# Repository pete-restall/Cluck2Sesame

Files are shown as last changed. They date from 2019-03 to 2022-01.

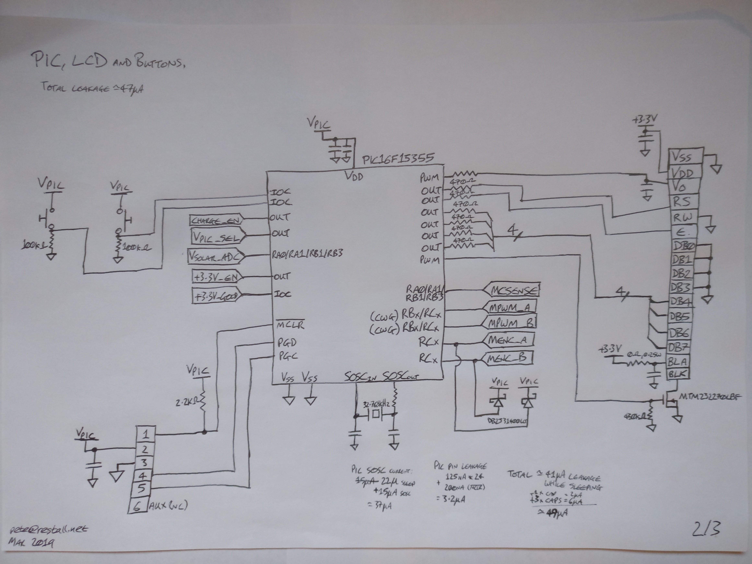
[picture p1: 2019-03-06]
doc/design/sketches/rough-circuit-outline-2.jpg

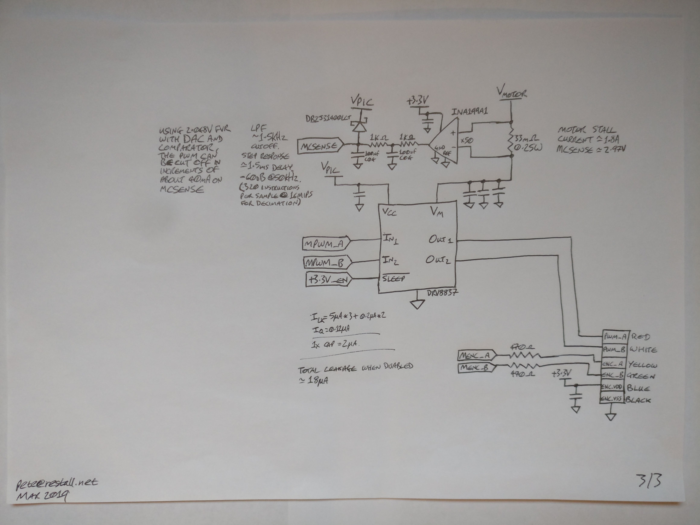
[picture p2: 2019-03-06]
doc/design/sketches/rough-circuit-outline-3.jpg

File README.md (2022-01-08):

# Cluck<sup>2</sup>Sesame - Yet Another Chicken Coop Door Opener (Revision II)

## What is it ?
It opens and closes the door of my wife's chicken coop based on Sunrise and
Sunset times so that she doesn't have to.  This is a refinement of the
[Cluck<sup>2</sup>Sesame](https://github.com/pete-restall/Cluck2Sesame-Prototype/)
project, building on lessons learned from the original attempt.  Notably:

 - The parts are not based on what I have lying around, but rather on parts
   selected for the job or known to do the job.  This has also simplified the
   design somewhat - more pins on the PIC mean the shift register is no longer
   required, for example.  The newer PIC is smaller, integrates more
   peripherals and comes with more flash; the original project ran out of
   flash before all features could be implemented.

 - The shortcomings in the end-of-travel detection, namely measuring motor
   current for stall torque, hastened battery depletion.  A rotary-encoder
   based approach will be used instead, which will hopefully lengthen battery
   life.

 - A solar charger will be included as replacing the battery, fairly regularly
   as it turned out, meant unscrewing the enclosure.

 - The motor will be a 6V model rather than a 12V model and run directly from 
   the battery rather than off an SMPS.  No SMPS means a smaller BOM and no
   power wasted by the high motor currents.  This should extend battery life
   even further, at the expense of varying speed.  But that's not an issue.

 - The PCB will be made in China, and the board house charges the same price
   regardless of whether the PCB is the size of the enclosure or the size of
   the LCD module.  This means that the aluminium backplate can be replaced
   with a PCB, providing more flexibility and space for layout and mounting
   while reducing the cost and time of the build.

That said, some of the parts from the original have been incorporated into
the newer design since they are known to work and are already stocked in my
parts bins.

## Why 'Cluck<sup>2</sup>Sesame' ?
Because 'Cluck Cluck Sesame' is obviously what the chickens would say if
they needed to open a door.

## The Hardware and Firmware
The hardware and firmware are all mine.  The board is based around a
[PIC16F15356](doc/datasheets/mcu/PIC16F15356.pdf).  It's a beefier evolution
of what was used last time that has allowed considerable simplification of the
board through more integration and a higher pin count.

## Pictures
None yet.  But there will be.

## Build


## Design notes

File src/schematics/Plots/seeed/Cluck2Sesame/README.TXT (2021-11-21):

Customer:
---------
Pete Restall (Parity Computer Consultancy Limited) - pete@restall.net
Any problems / questions, please do not hesitate to get in touch.

Design Tools Used:
------------------
DesignSpark 8.1.2
Gerbv 2.6.2

Track and Spacing:
------------------
Minimum 6mil.

Layers:
-------
All viewed from above, no mirroring.  Solder Resist and Solder Paste Stencil
layers are negatives, all others are positives.

Board Outline:
--------------
All layers contain a zero-width board outline.  Outline size is
4.24016in x 4.20000in and >= 20mil from any feature, copper or otherwise.

Vias and Silkscreen:
--------------------
Some vias are partially covered with silkscreen; this is not anticipated to
be an issue since they should be tented.

Pads and Silkscreen:
--------------------
Some silkscreen map overlap, but this is not an issue.  The silkscreen can be
clipped where necessary, but please advise if this is going to be an issue.

Drill Holes:
------------
All are through-plated and are finished sizes; no adjustments have been made
for plating thickness.  All are >= 20mil from the edge of the board.

Bit sizes can be rounded to the nearest 0.1mm.  Please advise if any drill
sizes are found to be incompatible with your processes.

Annular rings >= 6mil.  Holes >= 0.4mm.

Data Formats:
-------------
More detailed information can be found in "DesignSpark Plot Report.TXT", but
in summary:

Gerber Settings
===============

    Leading zero suppression.
    G01 assumed throughout.
    Line termination <*> <CR> <LF>.
    3.5 format absolute inches.
    Format commands defined in Gerber file.
    Aperture table defined in Gerber file.
    Hardware arcs allowed.

Drill Settings
==============

    Excellon Format 1
    Format 3.5 absolute in inches.
    Zero suppression Leading

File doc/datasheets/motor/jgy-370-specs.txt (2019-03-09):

=======================
From Aliexpress Website
=======================
1pcs DC6V 12V 24V JGY370 Large Torque Full Metal Gearbox Turbo Worm Gear Motor with Hall Encoder
Specification:
Note: Different parameters' motors have their different looks. The lower speed and higher voltage are, the larger the torque is. Please read the parameters table before buying. Thanks!!!

Voltage: DC6V, DC12V, DC24V

No-Load Speed: 6rpm, 10rpm, 18rpm, 23rpm, 30rpm, 40rpm, 90rpm, 150rpm

Error: ±10%

Output Shaft Diameter: 6mm D-type

Output Shaft Length: 14mm
Gearbox Size:46*32*25mm

Gearbox Size Detal, please see the table
Wirings:

Notice:  
1. The yellow and green wires are the speed signal output line, and they can't be connected any power supply, or it will be burnt.
2. Positive and negative power supply of encoder do not allow connect wrong;voltage is 3.3-5V.
3. Control CW or CCW of motor by changing the positive and negative power supply of encoder (change Red Wire and White Wire connect)

Red Wire - positive power supply of motor(+)

White Wire - negative power supply of motor(-)

Black Wire - negative power supply of encoder(-) (positive and negative power supply of encoder do not allow connect wrong;voltage is3.3-5V)

Blue Wire - positive power supply of encoder(+) (positive and negative power supply of encoder do not allow connect wrong;voltage is 3.3-5V)

Yellow Wire - signal feedback (11 signals per motor turns a circle)

Green Wire - signal feedback (11 signals per motor turns a circle)

========================
Measurements and Testing
========================
At 11 Celsius:

	+6.0V, 150mA unloaded, unable to stall with fingers
	+4.3V, 150mA unloaded, 1.5A stall
	+3.0V, 110mA unloaded, 900mA stall
	+2.5V, 100mA unloaded, 770mA stall
	+2.0V,  80mA unloaded, 615mA stall

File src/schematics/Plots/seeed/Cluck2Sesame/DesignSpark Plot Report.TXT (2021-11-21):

Plot Report
-----------

Report Written:     Sunday, November 21, 2021
Project Path:       Z:\home\pete\Projects\Cluck3Sesame\src\schematics\Cluck2Sesame.prj
Design Path:        Z:\home\pete\Projects\Cluck3Sesame\src\schematics\Cluck2Sesame.pcb
Design Title:       Cluck2Sesame PCB Layout
Created:            27/03/2019 19:50:45
Last Saved:         21/11/2021 18:45:09
Editing Time:       6089 min
Units:              mil (precision 2)

Device Settings
===============

Gerber Settings
===============

    Leading zero suppression.
    G01 assumed throughout.
    Line termination <*> <CR> <LF>.
    3.5 format absolute inches.

    Format commands defined in Gerber file.
    Aperture table defined in Gerber file.
    Hardware arcs allowed.

Drill Settings
==============

    Excellon Format 1    Format 3.5 absolute in mm.
    Zero suppression Leading

Plots Output
============

    Plot Job: "Z:\home\pete\Projects\Cluck3Sesame\src\schematics\Cluck2Sesame.mop"

Gerber Output
=============

Z:\home\pete\Projects\Cluck3Sesame\src\schematics\Plots\Cluck2Sesame - Top Silkscreen.gbr

    Layers:
    ------------------
    Top Silkscreen
    Board Outlines

    D-Code Shape  (thou)
    -----------------------
    D10    Round 5.00
    D11    Round 12.00
    D13    Round 0.00
    D77    Round 6.00
    D78    Round 20.00
    D79    Round 10.00

Gerber Output
=============

Z:\home\pete\Projects\Cluck3Sesame\src\schematics\Plots\Cluck2Sesame - Top Solder Mask.gbr

    Layers:
    -------------------
    Top Solder Mask
    Board Outlines

    D-Code Shape  (thou)
    ------------------------------------------
    D13    Round 0.00
    D80    Round 282.00
    D81    Round 216.00
    D82    Round 163.48
    D83    Square 74.00
    D84    Oval 68.99 X 100.49
    D85    Oval 66.00 X 116.00  Rotation 90
    D86    Square 69.00
    D87    Square 68.99

Gerber Output
=============

Z:\home\pete\Projects\Cluck3Sesame\src\schematics\Plots\Cluck2Sesame - Top Copper.gbr

    Layers:
    ------------------
    Top Copper
    Board Outlines

    D-Code Shape  (thou)
    ------------------------------------------
    D10    Round 5.00
    D11    Round 12.00
    D13    Round 0.00
    D88    Round 276.00
    D89    Round 210.00
    D90    Round 157.48
    D91    Square 68.00
    D92    Oval 62.99 X 94.49
    D93    Oval 60.00 X 110.00  Rotation 90
    D94    Square 63.00
    D95    Square 62.99
    D96    Round 28.00
    D97    Round 8.00

Gerber Output
=============

Z:\home\pete\Projects\Cluck3Sesame\src\schematics\Plots\Cluck2Sesame - Bottom Copper.gbr

    Layers:
    ------------------
    Bottom Copper
    Board Outlines

    D-Code Shape  (thou)
    ----------------------------------------------
    D10    Round 5.00
    D11    Round 12.00
    D13    Round 0.00
    D77    Round 6.00
    D78    Round 20.00
    D79    Round 10.00
    D88    Round 276.00
    D89    Round 210.00
    D90    Round 157.48
    D91    Square 68.00
    D92    Oval 62.99 X 94.49
    D93    Oval 60.00 X 110.00  Rotation 90
    D94    Square 63.00
    D95    Square 62.99
    D96    Round 28.00
    D97    Round 8.00
    D98    Rectangle 55.00 X 60.00
    D99    Rectangle 55.00 X 60.00  Rotation 90
    D100   Rectangle 9.06 X 27.56  Rotation 90
    D101   Rectangle 35.43 X 59.06
    D102   Rectangle 16.54 X 27.56
    D103   Rectangle 16.54 X 39.37
    D104   Rectangle 72.83 X 93.31  Rotation 90
    D105   Rectangle 31.50 X 35.43  Rotation 90
    D106   Rectangle 17.72 X 57.09
    D107   Rectangle 31.50 X 35.43
    D108   Round 9.84
    D109   Rectangle 7.87 X 31.50  Rotation 90
    D110   Rectangle 7.87 X 31.50
    D111   Square 92.52
    D112   Rectangle 23.62 X 47.24
    D113   Rectangle 35.43 X 35.43  Rotation 90
    D114   Rectangle 35.43 X 35.43
    D115   Rectangle 11.02 X 19.69  Rotation 90
    D116   Rectangle 35.43 X 62.99
    D117   Rectangle 15.75 X 23.62  Rotation 90
    D118   Rectangle 39.37 X 42.91  Rotation 90
    D119   Round 50.00
    D120   Round 9.00
    D121   Round 15.00

Gerber Output
=============

Z:\home\pete\Projects\Cluck3Sesame\src\schematics\Plots\Cluck2Sesame - Bottom Solder Mask.gbr

    Layers:
    ----------------------
    Bottom Solder Mask
    Board Outlines

    D-Code Shape  (thou)
    ----------------------------------------------
    D13    Round 0.00
    D80    Round 282.00
    D81    Round 216.00
    D82    Round 163.48
    D83    Square 74.00
    D84    Oval 68.99 X 100.49
    D85    Oval 66.00 X 116.00  Rotation 90
    D86    Square 69.00
    D87    Square 68.99
    D122   Rectangle 61.00 X 66.00
    D123   Rectangle 61.00 X 66.00  Rotation 90
    D150   Rectangle 15.06 X 33.56  Rotation 90
    D151   Rectangle 41.43 X 65.06
    D152   Rectangle 22.54 X 33.56
    D153   Rectangle 22.54 X 45.37
    D154   Rectangle 78.83 X 99.31  Rotation 90
    D155   Rectangle 37.50 X 41.43  Rotation 90
    D156   Rectangle 23.72 X 63.09
    D157   Rectangle 37.50 X 41.43
    D158   Round 15.84
    D159   Rectangle 13.87 X 37.50  Rotation 90
    D160   Rectangle 13.87 X 37.50
    D161   Square 98.52
    D162   Rectangle 29.62 X 53.24
    D163   Rectangle 41.43 X 41.43  Rotation 90
    D164   Rectangle 41.43 X 41.43
    D165   Rectangle 17.02 X 25.69  Rotation 90
    D166   Rectangle 41.43 X 68.99
    D167   Rectangle 21.75 X 29.62  Rotation 90
    D168   Rectangle 45.37 X 48.91  Rotation 90

Gerber Output
=============

Z:\home\pete\Projects\Cluck3Sesame\src\schematics\Plots\Cluck2Sesame - Bottom Silkscreen.gbr

    Layers:
    ---------------------
    Bottom Silkscreen
    Board Outlines

    D-Code Shape  (thou)
    -----------------------
    D10    Round 5.00
    D13    Round 0.00

Gerber Output
=============

Z:\home\pete\Projects\Cluck3Sesame\src\schematics\Plots\Cluck2Sesame - Bottom Paste Mask.gbr

    Layers:
    ---------------------
    Bottom Paste Mask
    Board Outlines

    D-Code Shape  (thou)
    ----------------------------------------------
    D12    Rectangle 49.00 X 54.00
    D13    Round 0.00
    D14    Rectangle 49.00 X 54.00  Rotation 90
    D15    Rectangle 3.06 X 21.56  Rotation 90
    D16    Rectangle 29.43 X 53.06
    D17    Square 57.00
    D18    Rectangle 10.54 X 21.56
    D19    Rectangle 10.54 X 33.37
    D70    Rectangle 66.83 X 87.31  Rotation 90
    D71    Rectangle 25.50 X 29.43  Rotation 90
    D20    Rectangle 11.72 X 51.09
    D21    Rectangle 25.50 X 29.43
    D22    Round 3.84
    D23    Rectangle 1.87 X 25.50  Rotation 90
    D24    Rectangle 1.87 X 25.50
    D25    Square 86.52
    D26    Round 0.04
    D27    Rectangle 17.62 X 41.24
    D28    Rectangle 29.43 X 29.43  Rotation 90
    D29    Rectangle 29.43 X 29.43
    D72    Rectangle 5.02 X 13.69  Rotation 90
    D73    Rectangle 29.43 X 56.99
    D74    Rectangle 9.75 X 17.62  Rotation 90
    D75    Rectangle 33.37 X 36.91  Rotation 90

NC Drill Output
===============

Z:\home\pete\Projects\Cluck3Sesame\src\schematics\Plots\Cluck2Sesame - Drill Data - [Through Hole].drl

    Output:
    ---------------------------
    Plated Round Drill Holes
    Plated Slots
    Plated Board Outlines

    Tool  Size       Count   ID
    ----------------------------------
    T001  0.40640 mm 105   F
    T002  0.50800 mm 22    D
    T003  0.91440 mm 10    E
    T004  1.10000 mm 2     C
    T005  1.90000 mm 6     B
    T006  3.04800 mm 15    A
    ----------------------------------
    Total            160
    ----------------------------------

Z:\home\pete\Projects\Cluck3Sesame\src\schematics\Plots\Cluck2Sesame - Drill Data - [Through Hole] (Unplated).drl

    Output:
    -----------------------------
    Unplated Round Drill Holes
    Unplated Slots
    Unplated Board Outlines

    Tool  Size       Count   ID
    ----------------------------------
    T001  0.63500 mm 1
    ----------------------------------
    Total            1
    ----------------------------------

Gerber Output
=============

Z:\home\pete\Projects\Cluck3Sesame\src\schematics\Plots\Cluck2Sesame - Drill Ident Drawing - [Through Hole].gbr

    Layers:
    ------------------
    [Through Hole]
    Board Outlines

Drill Ident Drawing
===================

    Drill Plated Size Shape ID
    -----------------------------------
    120   Y      100  Round A
    75    Y      100  Round B
    43    Y      100  Round C
    20    Y      100  Round D
    36    Y      100  Round E
    16    Y      100  Round F

    D-Code Shape  (thou)
    -----------------------
    D10    Round 5.00
    D13    Round 0.00
    D76    Round 100.00

Gerber Output
=============

Z:\home\pete\Projects\Cluck3Sesame\src\schematics\Plots\Cluck2Sesame - Board Outline.gbr

    Layers:
    ------------------
    Board Outlines

    D-Code Shape  (thou)
    -----------------------
    D13    Round 0.00

End Of Report.

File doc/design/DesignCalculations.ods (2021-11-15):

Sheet: Motor
Lifting a Weight
Weight (kg) | 0.5
Height (cm) | 40
Time to Raise (s) | 30
Mechanical Power Required (W) | 0.0654
Motor |  |  | Rapid 37-0142 | JGY-370-320
Output Power (W) | 0.33 | Datasheet parameter | 0.56 | 0.45
Current (mA) | 435 | Datasheet parameter | 360 | 230
Angular Speed (rpm) | 1200 | Datasheet parameter | 5200 | 7
Torque (g.cm) | 15 | Datasheet parameter | 10.5 | 1000
Efficiency | 30.00% | Datasheet parameter | 51.90% | 30.00%
Input Power (W) | 1.1 | Worm efficiency will be < 50%, so add a decent margin; also allow higher transient current when starting (overcome worm static friction)
Angular Speed (rads/s) | 125.663706143592
Torque (Nm) | 0.0014709975045
Gears
Worm Gear Reduction (1:N) | 40
Shaft / Pulley Diameter (mm) | 20
Torque of 0.5kg Weight on Pulley (Nm) | 0.04905
Angular Speed (rpm) | 30
Angular Speed (rads/s) | 3.14159265358979
Torque at Worm Gear (Nm) | 0.05883990018
Lifting Force (N) | 5.883990018
Lifting Weight (kg) | 0.599795108868501
Lifting Speed (mm/s) | 31.4159265358979
Time to Raise (s) | 12.7323954473516
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

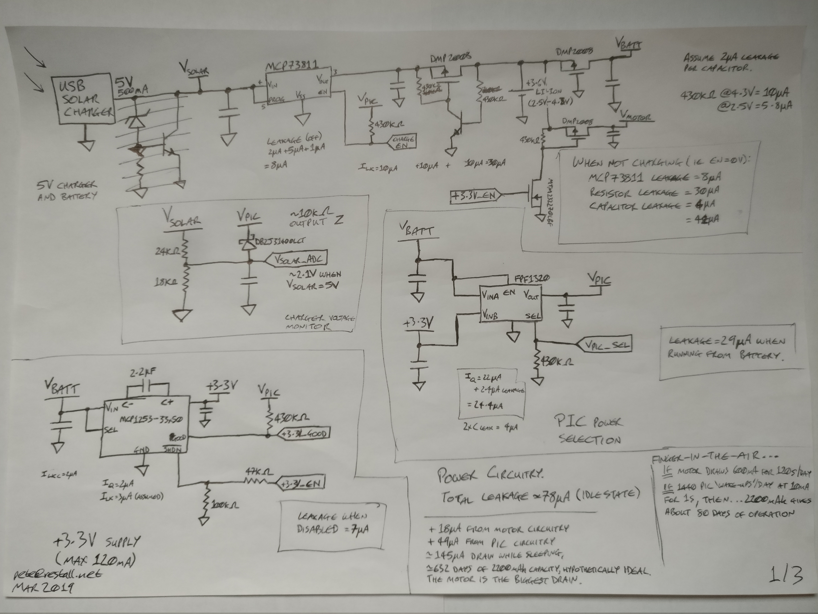
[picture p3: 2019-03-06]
doc/design/sketches/rough-circuit-outline-1.jpg

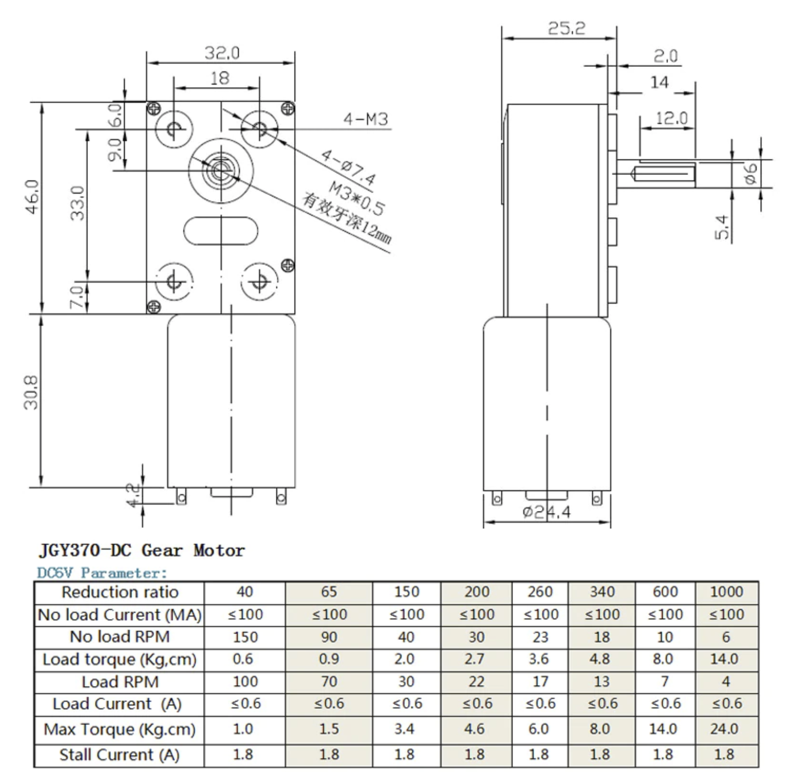
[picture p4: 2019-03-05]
doc/datasheets/motor/jgy-370-specs.png

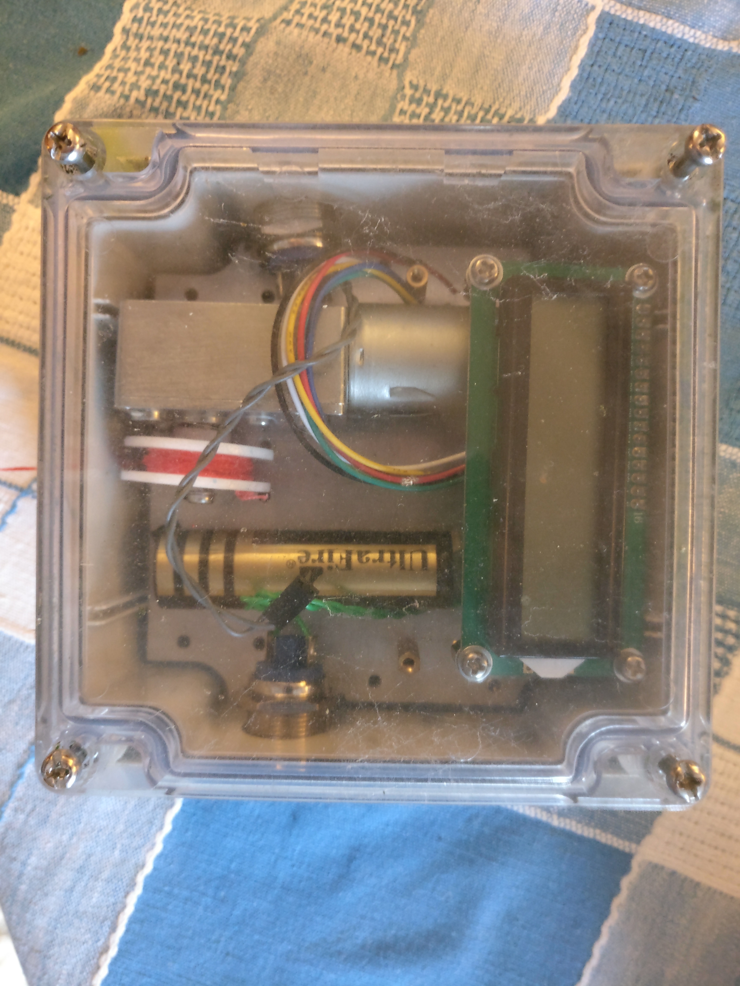
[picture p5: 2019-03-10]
doc/design/sketches/possible-layout.jpg

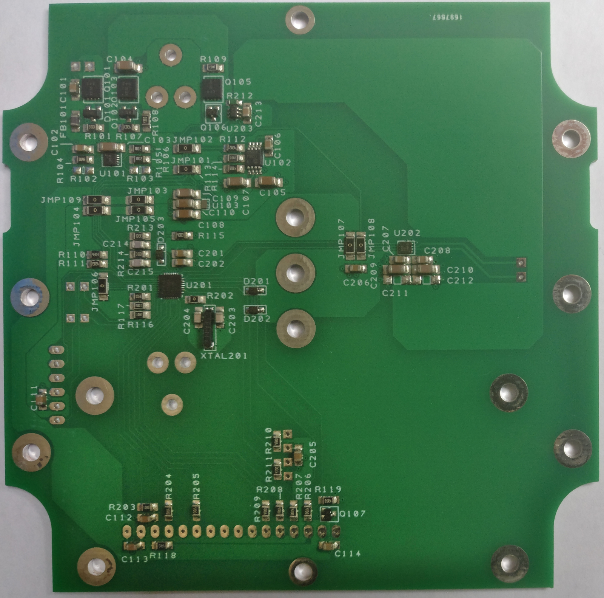
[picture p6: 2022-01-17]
doc/images/seeed-pcb-back-1600x1582.png

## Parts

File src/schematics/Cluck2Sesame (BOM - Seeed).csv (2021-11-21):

Ref Name | Package | Value | Height | Manufacturer | Manufacturer Part Number | Alternative Part Number | Supplier | Substitute Allowed ? | Substitution Notes
C101 | 0805 | 2.2uF | 1.35mm | Samsung | CL21B225KOFNNNE |  | Digikey
C102 | 0805 | 2.2uF | 1.35mm | Samsung | CL21B225KOFNNNE |  | Digikey
C103 | 1206 | 10uF | 1.8mm | Samsung | CL31B106KOHNNWE |  | Digikey
C104 | 1206 | 10uF | 1.8mm | Samsung | CL31B106KOHNNWE |  | Digikey
C105 | 1206 | 10uF | 1.8mm | Samsung | CL31B106KOHNNWE |  | Digikey
C106 | 0805 | 2.2uF | 1.35mm | Samsung | CL21B225KPFNNNE |  | Digikey
C107 | 1206 | 10uF | 1.8mm | Samsung | CL31B106KOHNNWE |  | Digikey
C108 | 1206 | 10uF | 1.8mm | Samsung | CL31B106KOHNNWE |  | Digikey
C109 | 1206 | 10uF | 1.8mm | Samsung | CL31B106KOHNNWE |  | Digikey
C110 | 1206 | 10uF | 1.8mm | Samsung | CL31B106KOHNNWE |  | Digikey
C111 | 0805 | 2.2uF | 1.35mm | Samsung | CL21B225KPFNNNE |  | Digikey
C112 | 0805 | 2.2uF | 1.35mm | Samsung | CL21B225KPFNNNE |  | Digikey
C113 | 0805 | 2.2uF | 1.35mm | Samsung | CL21B225KPFNNNE |  | Digikey
C114 | 0805 | 2.2uF | 1.35mm | Samsung | CL21B225KPFNNNE |  | Digikey
C201 | 0805 | 2.2uF | 1.35mm | Samsung | CL21B225KPFNNNE |  | Digikey
C202 | 0805 | 2.2uF | 1.35mm | Samsung | CL21B225KPFNNNE |  | Digikey
C203 | 0805 | 15pF | 1.35mm | Stackpole | CML0805C0G150JT50V |  | Digikey
C204 | 0805 | 15pF | 1.35mm | Stackpole | CML0805C0G150JT50V |  | Digikey
C205 | 0805 | 2.2uF | 1.35mm | Samsung | CL21B225KPFNNNE |  | Digikey
C206 | 0805 | 2.2uF | 1.35mm | Samsung | CL21B225KPFNNNE |  | Digikey
C207 | 0805 | 2.2uF | 1.35mm | Samsung | CL21B225KPFNNNE |  | Digikey
C208 | 0805 | 2.2uF | 1.35mm | Samsung | CL21B225KPFNNNE |  | Digikey
C209 | 1206 | 10uF | 1.8mm | Samsung | CL31B106KOHNNWE |  | Digikey
C210 | 1206 | 10uF | 1.8mm | Samsung | CL31B106KOHNNWE |  | Digikey
C211 | 1206 | DNP | 0.1mm
C212 | 1206 | DNP | 0.1mm
C213 | 0805 | 2.2uF | 1.35mm | Samsung | CL21B225KPFNNNE |  | Digikey
C214 | 0805 | 33nF | 1.45mm | TDK | C2012C0G2A333J125AC |  | Digikey
C215 | 0805 | 33nF | 1.45mm | TDK | C2012C0G2A333J125AC |  | Digikey
D101 | SOT23-2mm centres pins 1-3 |  | 1.5mm | ON Semi | BZX84C5V1LT3G |  | Digikey
D201 | SC-90A |  | 1mm | Nexperia | RB751V40,115 |  | Digikey
D202 | SC-90A |  | 1mm | Nexperia | RB751V40,115 |  | Digikey
D203 | SC-90A |  | 1mm | Nexperia | RB751V40,115 |  | Digikey
FB101 | 0805 |  | 1.1mm | TDK | MPZ2012S101AT000 |  | Digikey
JMP101 | 1206 | 0 | 1mm | Bourns | CR1206-J/-000ELF |  | Digikey
JMP102 | 1206 | 0 | 1mm | Bourns | CR1206-J/-000ELF |  | Digikey
JMP103 | 1206 | 0 | 1mm | Bourns | CR1206-J/-000ELF |  | Digikey
JMP104 | 1206 | 0 | 1mm | Bourns | CR1206-J/-000ELF |  | Digikey
JMP105 | 1206 | 0 | 1mm | Bourns | CR1206-J/-000ELF |  | Digikey
JMP106 | 1206 | 0 | 1mm | Bourns | CR1206-J/-000ELF |  | Digikey
JMP107 | 1206 | 0 | 1mm | Bourns | CR1206-J/-000ELF |  | Digikey
JMP108 | 1206 | 0 | 1mm | Bourns | CR1206-J/-000ELF |  | Digikey
JMP109 | 1206 | 0 | 1mm | Bourns | CR1206-J/-000ELF |  | Digikey
Q101 | POWERDI3333-8 |  | 1mm | Diodes Incorporated | DMP2008UFG |  | Digikey
Q102 | SOT23-BEC (2mm pad centres) |  | 1.5mm | ON Semi | MMBT6429LT1G |  | Digikey
Q103 | POWERDI3333-8 |  | 1mm | Diodes Incorporated | DMP2008UFG |  | Digikey
Q105 | POWERDI3333-8 |  | 1mm | Diodes Incorporated | DMP2008UFG |  | Digikey
Q106 | SOT323 (1_9mm pad centres) |  | 1.5mm | Nexperia | BSS138PW,115 |  | Digikey
Q107 | SOT323 (1_9mm pad centres) |  | 1.5mm | Nexperia | BSS138PW,115 |  | Digikey
R101 | 0805 | 3.3k | 0.6mm | Yageo | RC0805FR-073K3L |  | Digikey
R102 | 0805 | DNP | 0mm
R103 | 0805 | DNP | 0mm
R104 | 0805 | 560 | 0.6mm | Yageo | RC0805FR-07560RL |  | Digikey
R105 | 0805 | 10k | 0.6mm | Yageo | RC0805FR-0710KL |  | Digikey
R106 | 0805 | 10k | 0.6mm | Yageo | RC0805FR-0710KL |  | Digikey
R107 | 0805 | 430k | 0.6mm | Yageo | RC0805FR-07430KL |  | Digikey
R108 | 0805 | 430k | 0.6mm | Yageo | RC0805FR-07430KL |  | Digikey
R109 | 0805 | 100k | 0.6mm | Yageo | RC0805FR-07100KL |  | Digikey
R110 | 0805 | 430k | 0.6mm | Yageo | RC0805FR-07430KL |  | Digikey
R111 | 0805 | 430k | 0.6mm | Yageo | RC0805FR-07430KL |  | Digikey
R112 | 0805 | 47k | 0.6mm | Yageo | RC0805FR-0747KL |  | Digikey
R113 | 0805 | 100k | 0.6mm | Yageo | RC0805FR-07100KL |  | Digikey
R114 | 0805 | 430k | 0.6mm | Yageo | RC0805FR-07430KL |  | Digikey
R115 | 0805 | 430k | 0.6mm | Yageo | RC0805FR-07430KL |  | Digikey
R116 | 0805 | 100k | 0.6mm | Yageo | RC0805FR-07100KL |  | Digikey
R117 | 0805 | 100k | 0.6mm | Yageo | RC0805FR-07100KL |  | Digikey
R118 | 0805 | 47 | 0.6mm | Yageo | RC0805FR-0747RL |  | Digikey
R119 | 0805 | 430k | 0.6mm | Yageo | RC0805FR-07430KL |  | Digikey
R201 | 0805 | 3.3k | 0.6mm | Yageo | RC0805FR-073K3L |  | Digikey
R202 | 0805 | 0 | 0.6mm | Bourns | CR0805-J/-000ELF |  | Digikey
R203 | 0805 | 100 | 0.6mm | Yageo | RC0805FR-07100RL |  | Digikey
R204 | 0805 | 470 | 0.6mm | Yageo | RC0805FR-07470RL |  | Digikey
R205 | 0805 | 470 | 0.6mm | Yageo | RC0805FR-07470RL |  | Digikey
R206 | 0805 | 470 | 0.6mm | Yageo | RC0805FR-07470RL |  | Digikey
R207 | 0805 | 470 | 0.6mm | Yageo | RC0805FR-07470RL |  | Digikey
R208 | 0805 | 470 | 0.6mm | Yageo | RC0805FR-07470RL |  | Digikey
R209 | 0805 | 470 | 0.6mm | Yageo | RC0805FR-07470RL |  | Digikey
R210 | 0805 | 470 | 0.6mm | Yageo | RC0805FR-07470RL |  | Digikey
R211 | 0805 | 470 | 0.6mm | Yageo | RC0805FR-07470RL |  | Digikey
R212 | 0603 | 33m | 1mm | Susumu | RL0816T-R033-F |  | Digikey
R213 | 0805 | 3.3k | 0.6mm | Yageo | RC0805FR-073K3L |  | Digikey
R214 | 0805 | 3.3k | 0.6mm | Yageo | RC0805FR-073K3L |  | Digikey
U101 | WSON |  | 1mm | TI | BQ24040 |  | Digikey
U102 | MSOP |  | 1.5mm | Microchip | MCP1253-33X50 |  | Digikey
U103 | 6-WLCSP |  | 0.7mm | Fairchild | FPF1320UCX |  | Digikey
U201 | UQFN4x4 |  | 0.6mm | Microchip | PIC16F15356-I/MV |  | Digikey
U202 | 8-WSON |  | 1.2mm | TI | DRV8837DSG |  | Digikey
U203 | SC70-6 |  | 1.5mm | TI | INA199A1DCK |  | Digikey
XTAL201 | MC-146 |  | 1.8mm | Epson | MC-146 32.7680KA-A0 |  | Digikey

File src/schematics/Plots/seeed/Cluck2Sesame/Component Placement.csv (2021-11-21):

Ref Name | Package | Height | Centre X | Centre Y | Rotation
C101 | 0805 | 1.35mm | 650.00 | 750.00 | 0.00
C102 | 0805 | 1.35mm | 700.00 | 1175.00 | 90.00
C103 | 1206 | 1.8mm | 900.00 | 1164.60 | 90.00
C104 | 1206 | 1.8mm | 1025.00 | 600.00 | 90.00
C105 | 1206 | 1.8mm | 2025.00 | 1425.00 | 90.00
C106 | 0805 | 1.35mm | 2026.02 | 1163.39 | 0.00
C107 | 1206 | 1.8mm | 1800.00 | 1425.00 | 90.00
C108 | 1206 | 1.8mm | 1437.50 | 1648.00 | 90.00
C109 | 1206 | 1.8mm | 1437.50 | 1502.00 | 90.00
C110 | 1206 | 1.8mm | 1437.50 | 1575.00 | 90.00
C111 | 0805 | 1.35mm | 400.00 | 2950.00 | 0.00
C112 | 0805 | 1.35mm | 1135.70 | 3800.00 | 90.00
C113 | 0805 | 1.35mm | 1035.70 | 4000.00 | 90.00
C114 | 0805 | 1.35mm | 2435.70 | 4000.00 | 90.00
C201 | 0805 | 1.35mm | 1405.75 | 1923.01 | 90.00
C202 | 0805 | 1.35mm | 1405.75 | 1988.01 | 90.00
C203 | 0805 | 1.35mm | 1676.87 | 2375.00 | 0.00
C204 | 0805 | 1.35mm | 1523.13 | 2375.00 | 0.00
C205 | 0805 | 1.35mm | 2225.00 | 3355.00 | 0.00
C206 | 0805 | 1.35mm | 2637.50 | 2037.50 | 90.00
C207 | 0805 | 1.35mm | 2950.00 | 1975.00 | 90.00
C208 | 0805 | 1.35mm | 3110.00 | 1975.00 | 90.00
C209 | 1206 | 1.8mm | 2927.60 | 2043.00 | 90.00
C210 | 1206 | 1.8mm | 3134.60 | 2043.00 | 90.00
C213 | 0805 | 1.35mm | 1868.96 | 925.00 | 0.00
C214 | 0805 | 1.45mm | 1100.00 | 1860.00 | 90.00
C215 | 0805 | 1.45mm | 1100.00 | 1990.00 | 90.00
D101 | SOT23-2mm centres pins 1-3 | 1.5mm | 775.00 | 925.00 | 0.00
D201 | SC-90A | 1mm | 1925.00 | 2187.50 | 0.00
D202 | SC-90A | 1mm | 1925.00 | 2325.00 | 0.00
D203 | SC-90A | 1mm | 1252.87 | 1925.00 | 270.00
FB101 | 0805 | 1.1mm | 650.00 | 975.00 | 0.00
JMP101 | 1206 | 1mm | 1437.50 | 1325.00 | 90.00
JMP102 | 1206 | 1mm | 1437.50 | 1175.00 | 90.00
JMP103 | 1206 | 1mm | 1100.00 | 1538.00 | 90.00
JMP104 | 1206 | 1mm | 794.25 | 1612.00 | 90.00
JMP105 | 1206 | 1mm | 1100.00 | 1612.00 | 90.00
JMP106 | 1206 | 1mm | 837.50 | 2150.00 | 0.00
JMP107 | 1206 | 1mm | 2600.00 | 1875.00 | 0.00
JMP108 | 1206 | 1mm | 2675.00 | 1875.00 | 0.00
JMP109 | 1206 | 1mm | 794.25 | 1538.00 | 90.00
Q101 | POWERDI3333-8 | 1mm | 775.00 | 750.00 | 180.00
Q102 | SOT23-BEC (2mm pad centres) | 1.5mm | 1025.00 | 925.00 | 0.00
Q103 | POWERDI3333-8 | 1mm | 1025.00 | 750.00 | 180.00
Q105 | POWERDI3333-8 | 1mm | 1625.00 | 750.00 | 0.00
Q106 | SOT323 (1_9mm pad centres) | 1.5mm | 1625.00 | 925.00 | 0.00
Q107 | SOT323 (1_9mm pad centres) | 1.5mm | 2435.70 | 3775.00 | 270.00
R101 | 0805 | 0.6mm | 775.00 | 1025.00 | 90.00
R104 | 0805 | 0.6mm | 700.00 | 1250.00 | 90.00
R105 | 0805 | 0.6mm | 1100.00 | 1250.00 | 90.00
R106 | 0805 | 0.6mm | 1100.00 | 1175.00 | 90.00
R107 | 0805 | 0.6mm | 1025.00 | 1025.00 | 90.00
R108 | 0805 | 0.6mm | 1150.00 | 975.00 | 0.00
R109 | 0805 | 0.6mm | 1625.00 | 600.00 | 90.00
R110 | 0805 | 0.6mm | 794.25 | 1925.00 | 90.00
R111 | 0805 | 0.6mm | 794.25 | 1990.00 | 90.00
R112 | 0805 | 0.6mm | 1775.00 | 1175.00 | 90.00
R113 | 0805 | 0.6mm | 1775.00 | 1250.00 | 90.00
R114 | 0805 | 0.6mm | 1775.00 | 1325.00 | 90.00
R115 | 0805 | 0.6mm | 1405.75 | 1795.00 | 90.00
R116 | 0805 | 0.6mm | 1100.00 | 2355.00 | 90.00
R117 | 0805 | 0.6mm | 1100.00 | 2290.00 | 90.00
R118 | 0805 | 0.6mm | 1235.70 | 4000.00 | 90.00
R119 | 0805 | 0.6mm | 2435.70 | 3675.00 | 90.00
R201 | 0805 | 0.6mm | 1100.00 | 2225.00 | 90.00
R202 | 0805 | 0.6mm | 1500.00 | 2250.00 | 90.00
R203 | 0805 | 0.6mm | 1135.70 | 3725.00 | 90.00
R204 | 0805 | 0.6mm | 1285.70 | 3750.00 | 0.00
R205 | 0805 | 0.6mm | 1485.70 | 3750.00 | 0.00
R206 | 0805 | 0.6mm | 2285.70 | 3750.00 | 0.00
R207 | 0805 | 0.6mm | 2185.70 | 3750.00 | 0.00
R208 | 0805 | 0.6mm | 2085.70 | 3750.00 | 0.00
R209 | 0805 | 0.6mm | 1985.70 | 3750.00 | 0.00
R210 | 0805 | 0.6mm | 2075.00 | 3255.00 | 0.00
R211 | 0805 | 0.6mm | 2075.00 | 3455.00 | 0.00
R212 | 0603 | 1mm | 1775.00 | 850.00 | 90.00
R213 | 0805 | 0.6mm | 1100.00 | 1795.00 | 90.00
R214 | 0805 | 0.6mm | 1100.00 | 1925.00 | 90.00
U101 | WSON | 1mm | 900.00 | 1250.00 | 270.00
U102 | MSOP | 1.5mm | 1925.00 | 1250.00 | 180.00
U103 | 6-WLCSP | 0.7mm | 1570.70 | 1575.00 | 0.00
U201 | UQFN4x4 | 0.6mm | 1325.00 | 2150.26 | 90.00
U202 | 8-WSON | 1.2mm | 2992.60 | 1889.96 | 90.00
U203 | SC70-6 | 1.5mm | 1775.00 | 925.00 | 90.00
XTAL201 | MC-146 | 1.8mm | 1600.00 | 2450.00 | 270.00

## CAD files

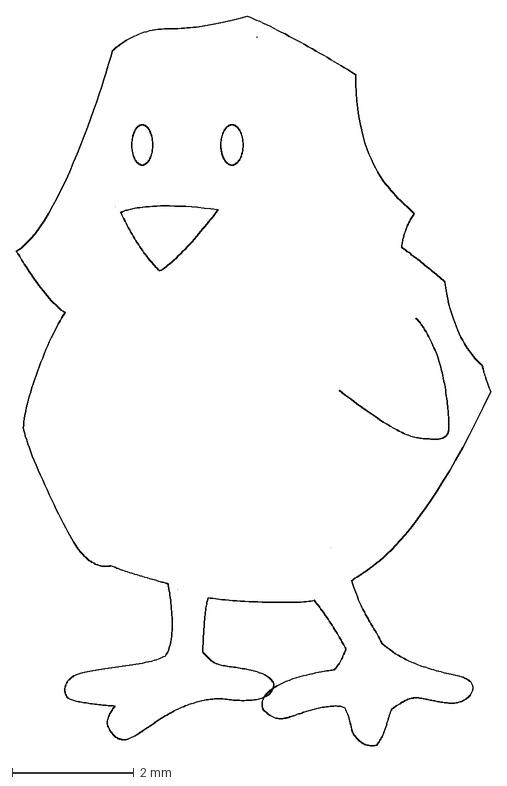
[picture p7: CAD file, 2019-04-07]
chick.dxf
7.80 x 12.0 mm

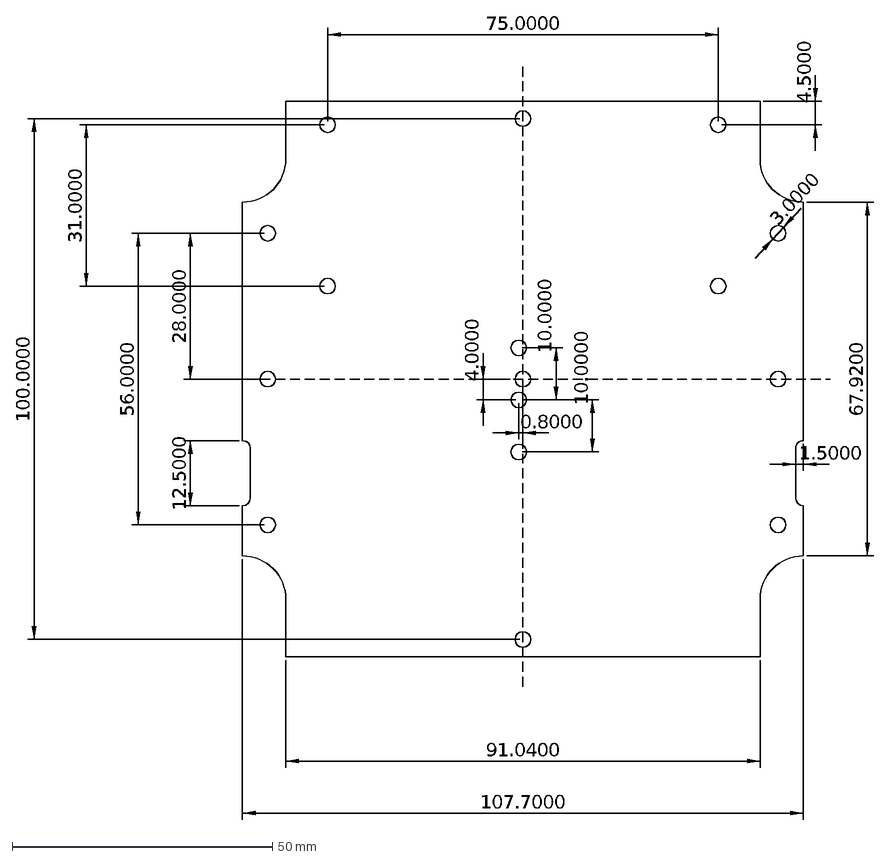
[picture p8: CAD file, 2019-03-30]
src/drawings/BackPlate.dxf
3.0000
28.0000
56.0000
100.0000
107.7000
91.0400
67.9200
12.5000
1.5000
75.0000
31.0000
4.5000
10.0000
4.0000
0.8000

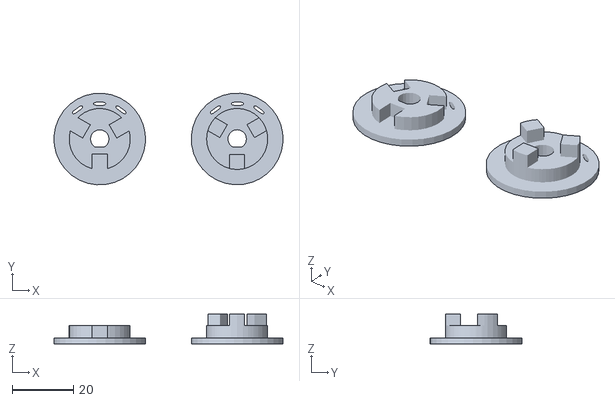
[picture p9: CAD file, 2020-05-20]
src/models/cluck2sesame-spool.stl
75.0 x 30.0 x 9.80

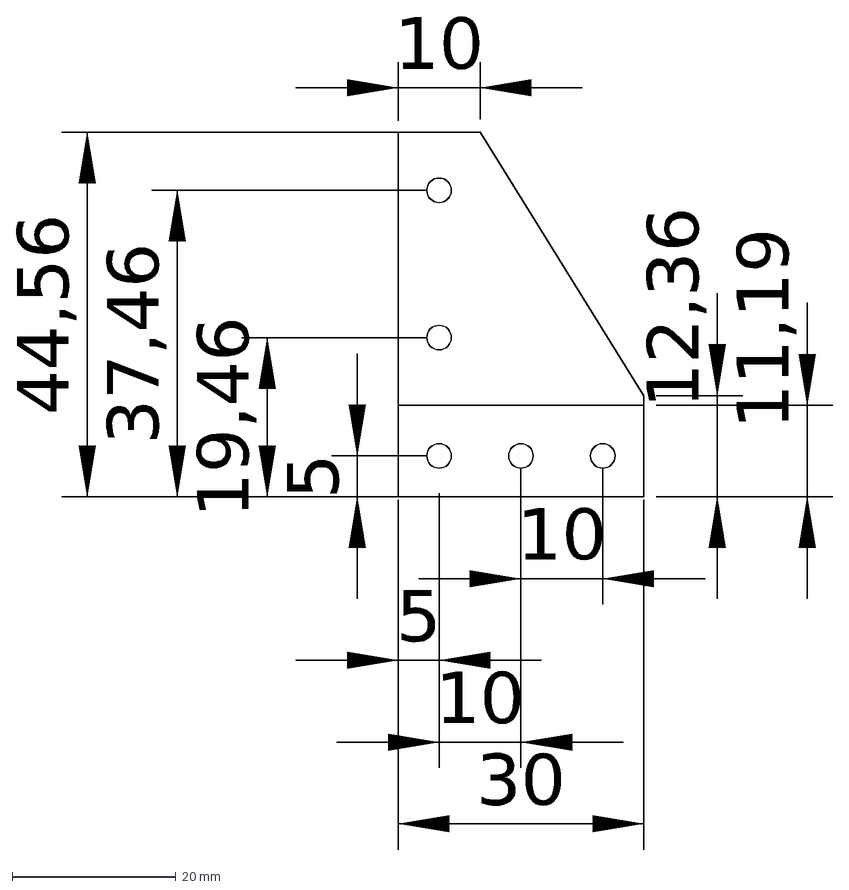
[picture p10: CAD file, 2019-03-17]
src/drawings/MotorBracket.dxf
5
19,46
37,46
44,56
11,19
12,36
10
30

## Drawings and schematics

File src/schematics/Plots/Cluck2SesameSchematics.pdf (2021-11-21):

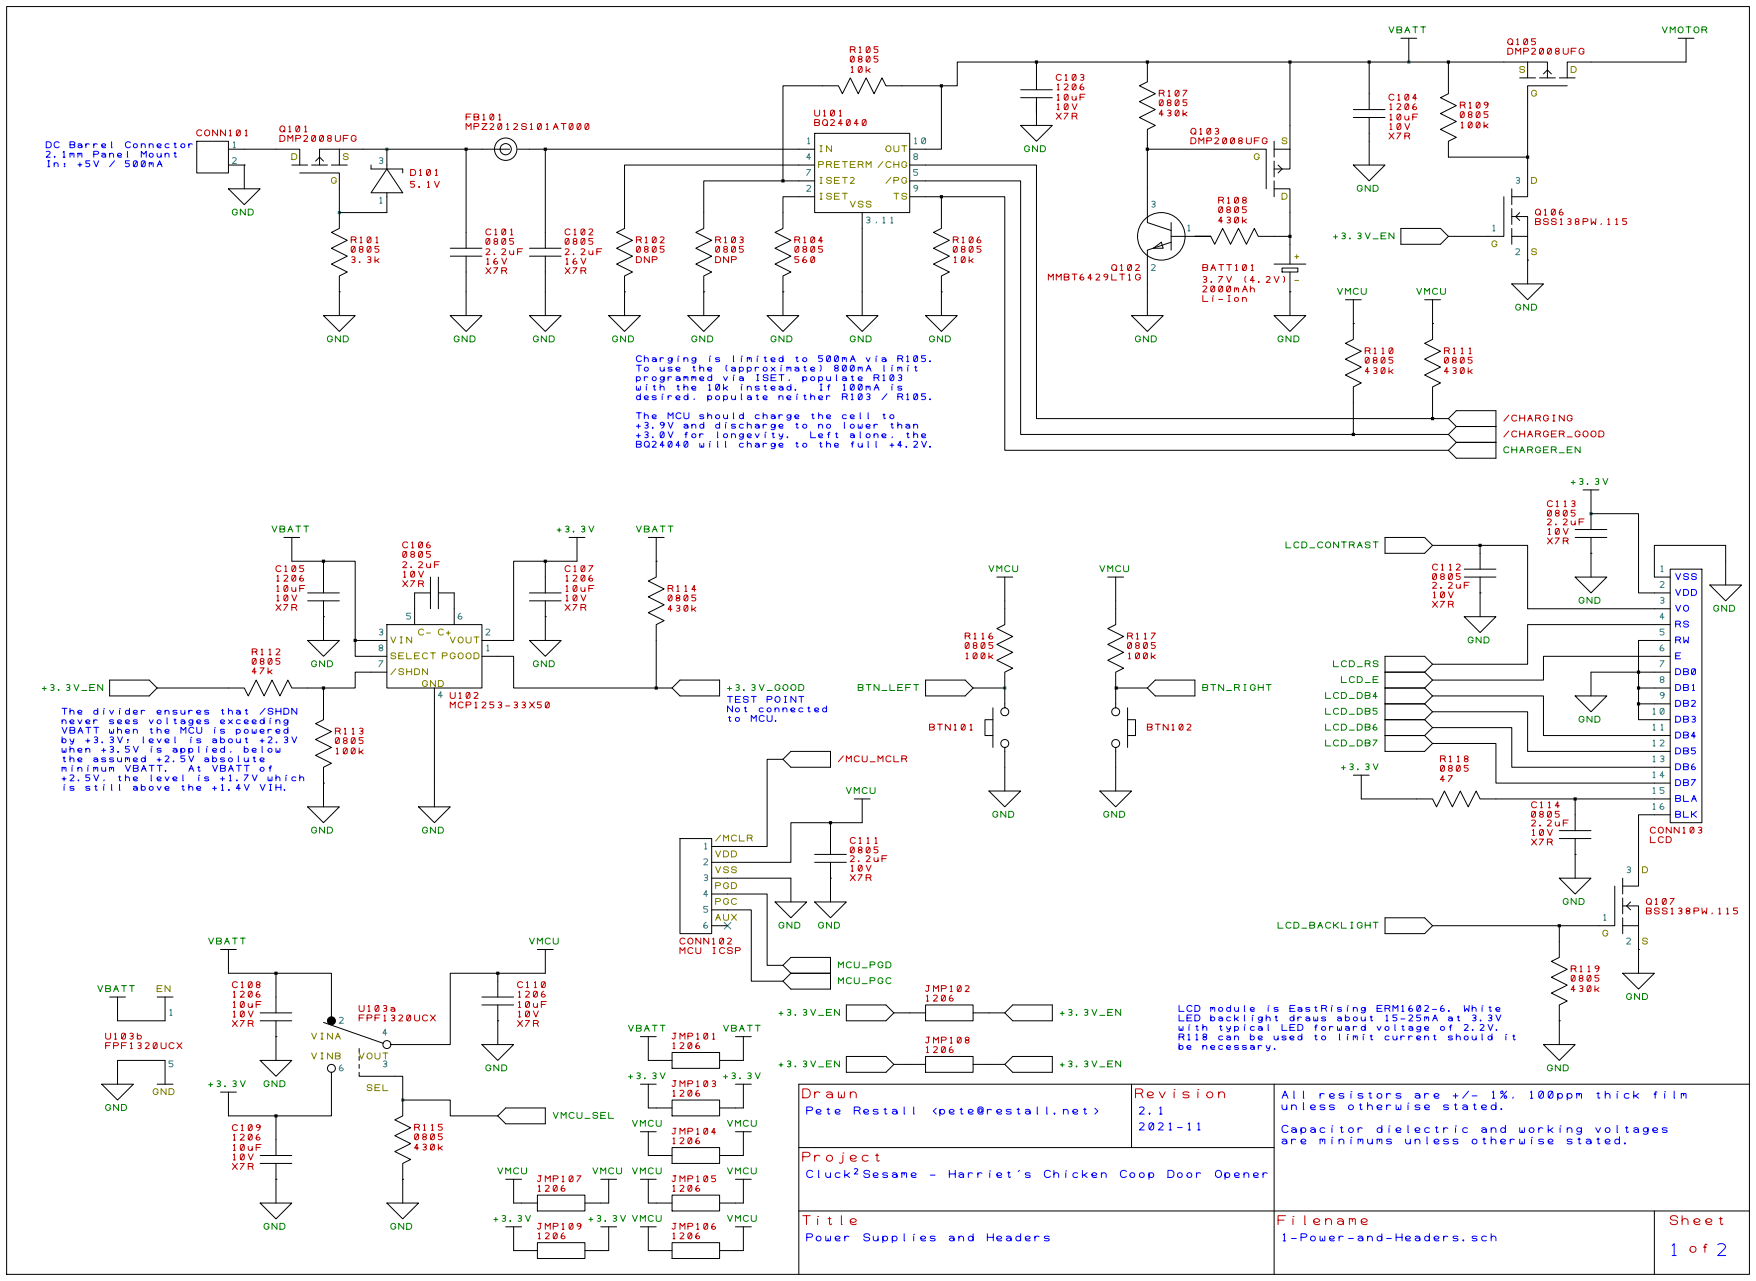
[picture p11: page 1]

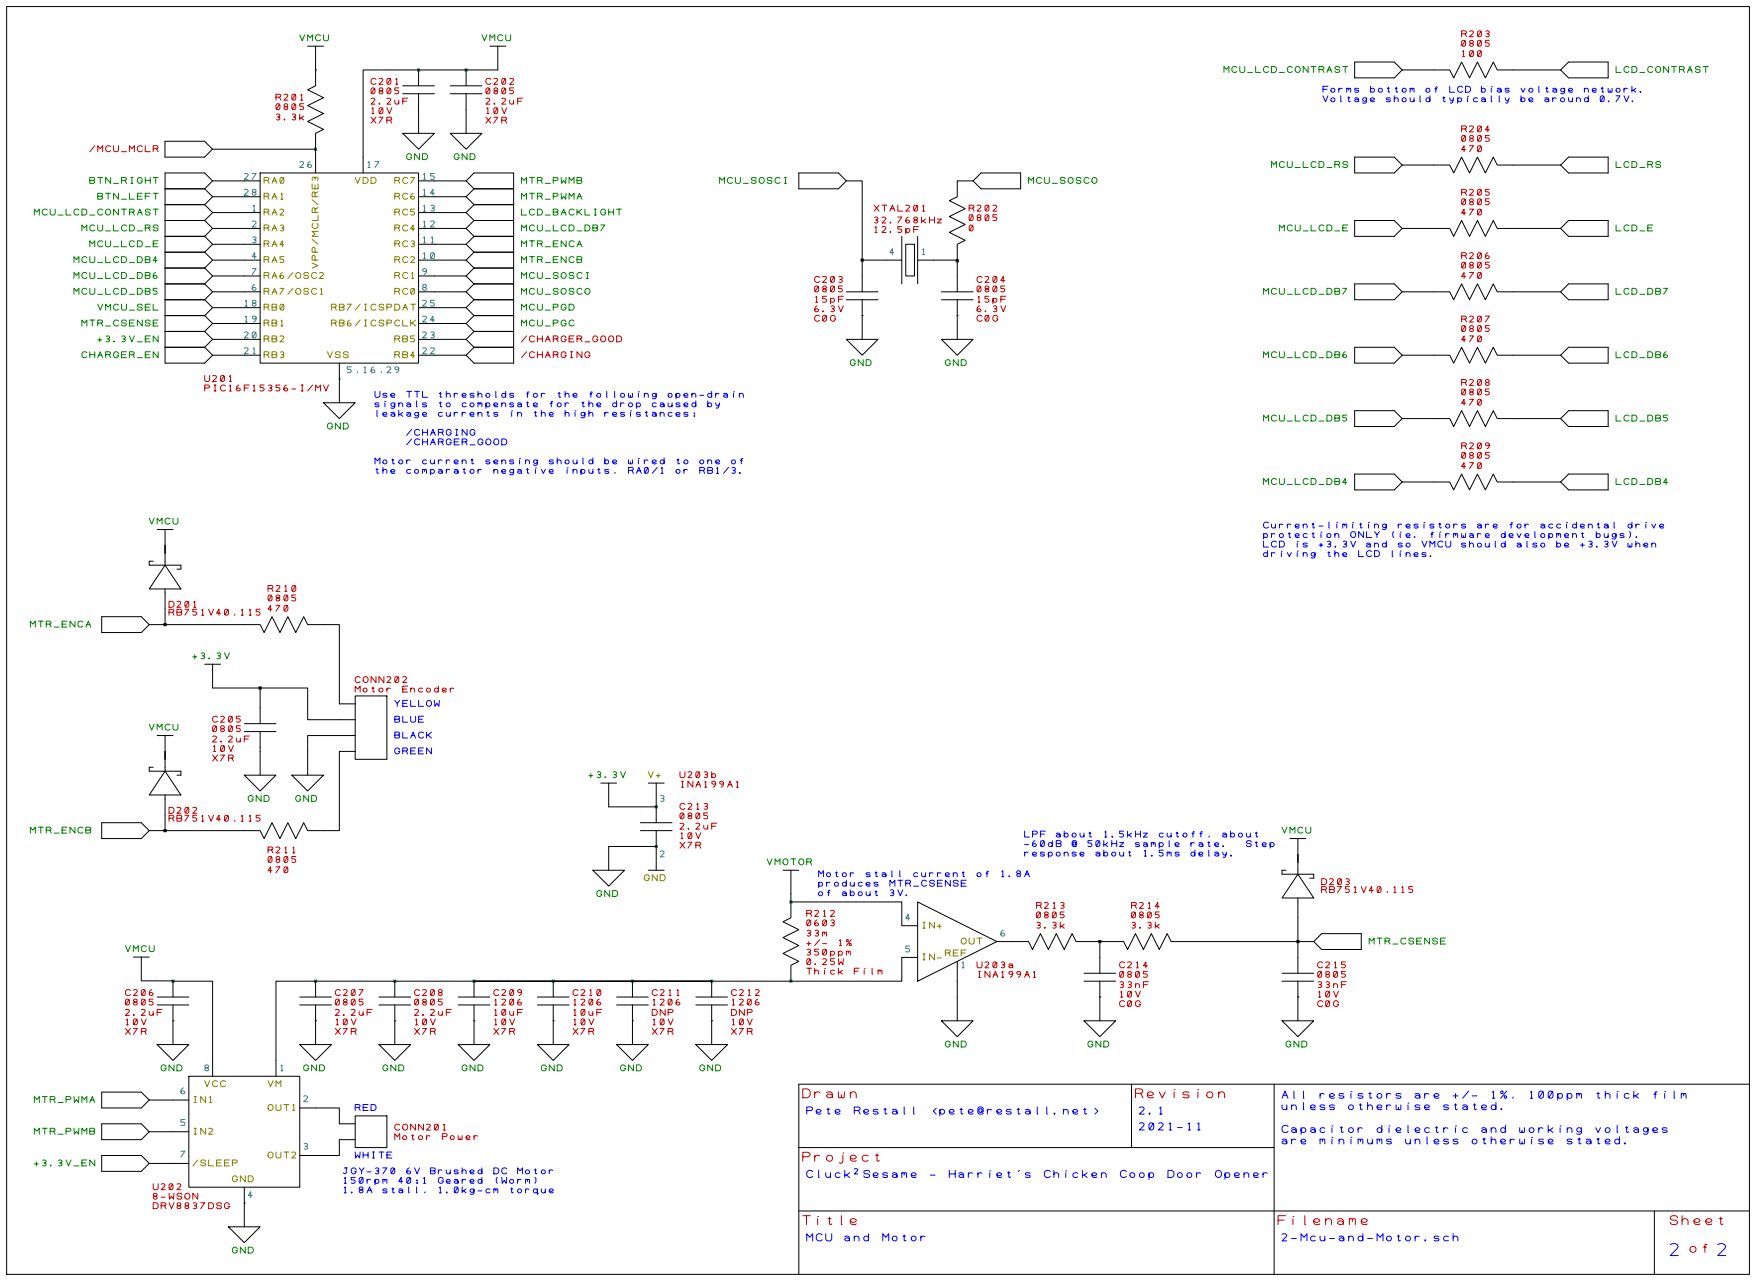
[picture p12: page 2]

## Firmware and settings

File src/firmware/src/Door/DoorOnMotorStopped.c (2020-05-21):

#include <xc.h>
#include <stdint.h>

#include "../Platform/NvmSettings.h"
#include "../Platform/Motor.h"
#include "../ApplicationNvmSettings.h"

#include "Door.h"

void doorOnMotorStopped(const struct Event *event)
{
	const struct MotorStopped *args = (const struct MotorStopped *) event->args;
	uint8_t fault = 0;
	switch (doorState.current)
	{
		case DoorState_Opening:
			if (args->fault.any)
			{
				if (args->fault.currentLimited)
					fault = DOOR_JAMMED;

				goto motorFaulted;
			}

			if (doorState.transition != DoorTransition_Close)
			{
				motorDisable();
				doorState.current = DoorState_Opened;
				doorState.transition = DoorTransition_Unchanged;
				eventPublish(DOOR_OPENED, &doorState.opened);
			}
			else
			{
				eventPublish(DOOR_OPENED, &doorState.opened);
				doorStartClosing(DoorState_Closing, DoorState_Closing);
			}

			break;

		case DoorState_Closing:
			doorState.closed.loweredHeight -= args->actualCount;
			if (args->fault.any)
			{
				if (args->fault.currentLimited)
					fault = DOOR_REVERSED;

				goto motorFaulted;
			}

			if (doorState.transition != DoorTransition_Open)
			{
				motorDisable();
				doorState.current = DoorState_Closed;
				doorState.transition = DoorTransition_Unchanged;
				eventPublish(DOOR_CLOSED, &doorState.closed);
			}
			else
			{
				eventPublish(DOOR_CLOSED, &doorState.closed);
				doorStartOpening(DoorState_Opening, DoorState_Opening);
			}

			break;

		case DoorState_FindBottom:
			doorState.closed.loweredHeight -= args->actualCount;
			if (args->requestedCount < 0)
			{
				if (args->fault.any)
				{
					if (args->fault.currentLimited)
						fault = DOOR_REVERSED;

					goto motorFaulted;
				}

				motorOn(FIND_BOTTOM_RAISING);
				doorState.findBottomIterations++;
			}
			else
			{
				if (args->fault.currentLimited)
				{
					if (args->actualCount > FIND_BOTTOM_THRESHOLD)
					{
						eventPublish(DOOR_CLOSED, &doorState.closed);
						if (doorState.transition != DoorTransition_Open)
						{
							motorDisable();
							doorState.current = DoorState_Closed;
							doorState.transition = DoorTransition_Unchanged;
						}
						else
						{
							doorStartOpening(DoorState_Opening, DoorState_Opening);
						}
					}
					else
					{
						if (doorState.findBottomIterations == MAX_FIND_BOTTOM_ITERATIONS)
						{
							fault = LINE_TOO_LONG;
							goto motorFaulted;
						}

						motorOn(FIND_BOTTOM_LOWERING);
					}
				}
				else
				{
					if (args->fault.all == 0 || args->fault.encoderOverflow)
						fault = LINE_SNAPPED;

					goto motorFaulted;
				}
			}

			break;

		case DoorState_ManualOpening:
			if (args->fault.any)
			{
				if (args->fault.currentLimited)
					fault = DOOR_JAMMED;

				goto motorFaulted;
			}

			motorDisable();
			doorState.current = DoorState_Unknown;
			break;

		case DoorState_ManualClosing:
			if (args->fault.any)
			{
				if (args->fault.currentLimited)
					fault = DOOR_REVERSED;

				goto motorFaulted;
			}

			motorDisable();
			doorState.current = DoorState_Unknown;
			break;

		case DoorState_Fault:
		case DoorState_Unknown:
			break;

		case DoorState_Opening_WaitingForEnabledMotor:
		case DoorState_Closing_WaitingForEnabledMotor:
		case DoorState_ManualOpening_WaitingForEnabledMotor:
		case DoorState_ManualClosing_WaitingForEnabledMotor:
			motorDisable();

		default:
			doorState.current = DoorState_Unknown;
	};

	return;

motorFaulted:
	if (fault == 0)
	{
		if (args->fault.encoderTimeout)
			fault = ENCODER_BROKEN;

		if (args->fault.encoderOverflow)
			fault = LINE_TOO_LONG;
	}

	motorDisable();
	doorState.current = DoorState_Fault;
	doorState.aborted.fault.all = fault;
	eventPublish(DOOR_ABORTED, &doorState.aborted);
}

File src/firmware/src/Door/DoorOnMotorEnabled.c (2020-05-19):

#include <xc.h>
#include <stdint.h>

#include "../Platform/NvmSettings.h"
#include "../Platform/Motor.h"
#include "../ApplicationNvmSettings.h"

#include "Door.h"

void doorOnMotorEnabled(const struct Event *event)
{
	switch (doorState.current)
	{
		case DoorState_Opening_WaitingForEnabledMotor:
			doorStartOpening(DoorState_Opening, DoorState_Unknown);
			break;

		case DoorState_Closing_WaitingForEnabledMotor:
			doorStartClosing(DoorState_Closing, DoorState_Unknown);
			break;

		case DoorState_FindBottom_WaitingForEnabledMotor:
			doorStartFindingBottom(DoorState_FindBottom, DoorState_Unknown);
			break;

		case DoorState_ManualOpening_WaitingForEnabledMotor:
			doorStartOpening(DoorState_ManualOpening, DoorState_Unknown);
			break;

		case DoorState_ManualClosing_WaitingForEnabledMotor:
			doorStartClosing(DoorState_ManualClosing, DoorState_Unknown);
			break;

		default:
			doorState.current = DoorState_Unknown;
	};
}

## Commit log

2019-03-06 Added rough sketches of the circuit and an empty directory for the schematics.
2019-03-08 Created DesignSpark project.
    [1-Power.sch, BLANK-TEMPLATE.sch]
2019-03-09 Started drawing up the schematics. Added some quick motor measurements.
    [1-Power.sch]
2019-03-10 Work on the power supply schematics. Added a photo of a possible layout utilising the existing enclosure.
    [1-Power.sch]
2019-03-12 Work on the power supply schematics.
    [1-Power-and-Headers.sch, 1-Power.sch]
2019-03-13 Work on the schematics.
    [1-Power-and-Headers.sch, 2-Mcu-and-Motor.sch]
2019-03-17 Added mechanical drawings.
    [BackPlate.dxf, MotorBracket.dxf]
2019-03-17 Various design calculations.
    [DesignCalculations.ods]
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2019-03-24 Amended toolpath depths to 3mm to ensure a clean drill / edge.
2019-03-24 Added motor bracket holes and cut-outs for the button nuts.
    [BackPlate.dxf]
2019-03-30 Work on the PCB, starting with motor, cell, button, LCD and connector positions.
    [1-Power-and-Headers.sch, 2-Mcu-and-Motor.sch, BackPlate.dxf]
2019-03-30 Work on the PCB.
    [1-Power-and-Headers.sch, 2-Mcu-and-Motor.sch]
2019-04-09 Added PCB plots and manufacturing files.
    [1-Power-and-Headers.sch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]
2019-04-10 BOM tweaks.
    [1-Power-and-Headers.sch, 2-Mcu-and-Motor.sch]
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2019-04-14 Power management routine to put the device to sleep when there is nothing to do.
2019-04-18 Amended power consumption calculations to take into account the more frequent wake-from-sleep that becomes necessary because the timer postscalers can't be read.
    [DesignCalculations.ods]
2019-04-26 Fixed some silkscreen issues.
2019-04-26 Switched the order of C209-212 as the layout indicated C209-10 as being the closest to the DRV8837, but in reality they were swapped. Also bumped the revision to 1.1 along with a new date.
    [1-Power-and-Headers.sch, 2-Mcu-and-Motor.sch]
2019-04-26 Added missing +3.3V copper pour.
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2019-04-28 Added a Near Scheduler module, which will allow events to be published at 10ms intervals up to about 2.5 seconds away. It is intended as a way to implement timeouts and delays when interacting with p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
    [Initialise.c]
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2019-05-01 Modified Near Scheduler to use callbacks rather than publishing events, as this will simplify scenarios that need to publish events conditionally (ie. the Voltage Regulator Enabled event should not b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
2019-05-01 Disabling the NCO when it is no longer needed for near-scheduling. Put a TODO into the Voltage Regulator module to use the Near Scheduler to wait for the +3.3V rail to stabilise.
2019-05-01 Started to add callbacks for when the voltage rail has stabilised.
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2019-05-03 Work on enabling the Voltage Regulator, including splitting the tests into multiple files due to running out of space.
2019-05-03 Added a PWM Timer (TMR2) to the initialisation sequence. Fixed the NvmSettings psect linker issues.
    [Initialise.c, NvmSettings.c]
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2019-05-05 Added an LCD integration test fixture as it's probably the easiest way to test interaction with the display through the simulator. This will probably morph into a more general integration test fixtur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
    [NvmSettings.c]
2019-05-11 Fixed the justification of the LCD's contrast and brightness PWM duty-cycles.
2019-05-12 R203 changed from 3.3k to 100 ohms as it wasn't stiff enough to drive the bottom of the LCD's divider.
    [2-Mcu-and-Motor.sch]
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2019-05-12 Adjusted the LCD fixture timings to ensure more margin, which can occur due to +/- 5% HFINTOSC over temperature, as well as 32.768kHz crystal drift and the LCD module's oscillator innacuracies (nomin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
2019-05-19 Updated estimated power consumption figures now that the MCU wakes from sleep every minute rather than every four.
    [DesignCalculations.ods]
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2019-05-25 Motor pin direction changes when the voltage regulator is enabled / disabled. Necessary because if they are left as inputs then they would float when the +3.3V portion of the circuit is off.
2019-05-25 The Power Management module now disables all peripherals by default and it is up to the individual modules to re-enable them if they use them. A common 'Fixture.c' was added to allow testing of this 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
    [Initialise.c]
2019-05-26 MCU modules (peripherals) used by the motor are now being enabled / disabled with the voltage regulator.
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2019-05-26 Bugfix - corrected the polarity of the Current-Sense Comparator.
2019-05-26 Added the CLC configuration. Also a bugfix for the CWG auto-shutdown, which is active-low and not active-high as I was previously attempting.
    [NvmSettings.c]
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2019-05-30 Resetting the CCP module in motorOn() to prevent the shutdown / turn deadlock.
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2019-05-30 Split out the tests due to space constraints. Added the first couple of motorOff() tests.
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2019-06-02 PWM duty-cycle bugfix - stopping at 0xff caused spikes because the output flop's S and R were active very close to each other; a limit of 0x100 avoids the PWM4DCH comparator from matching, so the R i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
2019-06-02 Added a diagram illustrating the flow required for setting the door's open and close times.
2019-06-12 Bugfix - now implements the flowchart design properly to ensure the events will be fired off correctly.
    [DoorInitialise.c]
2019-06-13 Upgraded XC8 to v2.05 - finally figured out that the '*const' modifier on pointers causes it to lose track of references.
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2019-06-23 Added motor current limiting for the no-load scenario, required to find the bottom of travel when starting from an unknown position.
2019-06-26 Started work on turning the motor on but ran out of space so split the tests into separate files.
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2019-06-28 Started to add the MotorStopped behaviour for the Opening state of the Door's state machine.
2019-06-29 Added faults to the MotorStopped behaviour of the Opening state of the Door's state machine.
2019-06-29 Started to add reversal to the MotorStopped behaviour of the Opening state of the Door's state machine.
    [Door.h, DoorOnMotorStopped.c]
2019-06-29 Added reversal (Opened -> Closing) to the MotorStopped behaviour of the Opening state of the Door's state machine.
    [Door.h, DoorOnCloseScheduleActioned.c, DoorOnMotorStopped.c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]
2019-06-29 Added the MotorStopped behaviour of the Closing state of the Door's state machine.
2019-08-22 Bugfix - LINE_SNAPPED fault not being set when the motor stops without a fault when raising in DoorState_FindBottom.
    [DoorOnMotorStopped.c]
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2019-08-24 Reverted bench-testing modifications that were accidentally committed.
    [NvmSettings.c]
2020-05-10 Hacks from bench testing to fix motor direction and over-current issues.
2020-05-10 Some motor control bugfixes from bench testing the real hardware. The tests will need amending to take account of these.
    [DoorOnMotorStopped.c]
2020-05-12 More explicit height / distance constants, based on the spool and gearbox properties.
2020-05-12 A whole host of motor changes based off bench testing and tweaking. This has broken a lot of the tests because of the complexity of dealing with a non-idealised real-world - will figure out what to d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
2020-05-13 Tri-stating the LCD contrast pin when the LCD is not turned on. It cannot be 0V because that turns the screen dark. It cannot be +3.3V because if the LCD is off then we are driving current through th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
2020-05-13 Adjusted the power consumption calculations to reflect some measured values.
    [DesignCalculations.ods]
2020-05-14 Started to add the UI - button detection and screen on / off / timeout.
2020-05-15 Bugfix - sometimes the LCD latches were not at 0V when the regulator was off so the pins were powering the +3.3V rail via the LCD's protection diodes...
2020-05-15 Bugfix - the numberOfPendingSchedules counter was being incremented even when updating an already-pending schedule, which meant that the NCO never got disabled. This is about another 350uA worth of c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
2020-05-16 Initial door height set to 0 to force calibration. Manual door entry is the default until after calibration and setting the time, to avoid unwanted attempts at raising / lowering.
    [NvmSettings.c]
2020-05-16 Bugfix - when the screen is off and a button is pressed there should be no effect other than the screen turning on. Handlers for button release were executed regardless.
2020-05-18 Removed the TODO relating to coasting as the motor is now braked instead.
2020-05-19 Added a 3D printed spool to replace the CNC'd spool.
    [cluck2sesame-spool.stl]
2020-05-19 Started the motor PWM duty cycle off at a non-zero value to speed up the response, since most of the low duty cycles cannot overcome the static friction anyway.
2020-05-19 Bugfix - was mis-counting the voltage regulator enables and disables, leaving it on after the motor had been run and disabled.
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2020-05-20 Updated the spool based on some experimentation.
    [cluck2sesame-spool.stl]
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2021-09-13 Bugfix for rounding motor movements to nearest integer when given a negative value.
    [Door.h]
2021-11-15 Amended the LCD initialisation tests to tack account of the tristated contrast pin.
2021-11-15 Fixed the LCD tests by allowing a 100us 'glitch period' when bus lines are driven low at the same time as EN but just before the voltage regulator is disabled.
2021-11-15 Fixed typo with the LCD contrast pin assignment.
2021-11-15 Minor power calculation tweaks.
    [DesignCalculations.ods]
2021-11-15 Started to add the Battery module for monitoring and charging the lithium cell.
2021-11-19 Corrected the sampling order and timings for the periodic monitoring.
    [PeriodicMonitor.c]
2021-11-21 Replaced obsolete parts with substitutes. Started to put together the manufacturing package for Seeed. Renamed Cluck3Sesame to Cluck2Sesame and bumped the version number instead.
    [1-Power-and-Headers.sch, 2-Mcu-and-Motor.sch, Cluck2Sesame (BOM - Seeed).csv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]
2021-11-21 General Design Spark churn...
    [1-Power-and-Headers.sch, 2-Mcu-and-Motor.sch]
2021-11-21 Added the component placement and Seeed BOM based on their template.
    [Cluck2Sesame (Component Placement).csv, Cluck2Sesame BOM.xlsx]
2021-11-21 Added the BOM and component placement to the Seeed manufacturing package.
    [Component Placement.csv]
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2021-12-04 Added flags to allow the voltage reference and acquisition time to be altered for ADC conversions.
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2021-12-06 Amended the build scripts because the non-zero 'cat failure log' exit code was being propagated to the pipeline when it shouldn't have been (non-zero indicates no failure logs in this case).
2021-12-06 UpdatedUpgraded XC8 from 2.05 to 2.32, and fixed some errors and warnings in the process.
    [DoorCalibrate.c, DoorOnCloseScheduleActioned.c, DoorOnOpenScheduleActioned.c]
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2021-12-19 Added an '=' prefix to the sampled parameters since a hex 'e' could be mistaken for an error.
    Rejigged the fake UART1 test fixture a bit to prevent the hanging test.
    [CalibrationMode.c, CalibrationMode.h]
2021-12-20 Normalised the 'OK' response with the other non-error responses.
    [CalibrationMode.c, CalibrationMode.h]
2021-12-21 Added the 'REFCLK' command to the Calibration Mode. This involved various tweaks to the UART1 test fixture to solve memory overlay issues and SCL / code timing problems when running multiple tests.
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2021-12-21 Added 'REFCLK' command - file missed from previous commit.
    [CalibrationMode.c]
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
